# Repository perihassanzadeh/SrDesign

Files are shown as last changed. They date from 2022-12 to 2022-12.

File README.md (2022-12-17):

# Rubik's Cube Solver
System to automatically solve a Speed cube from any state

The system requirements were:
- Use Computer Vison to capture the current state of the cube
- Develop a non-trivial solving algorithm
- Use motors to actuate the faces of the cube to solve it

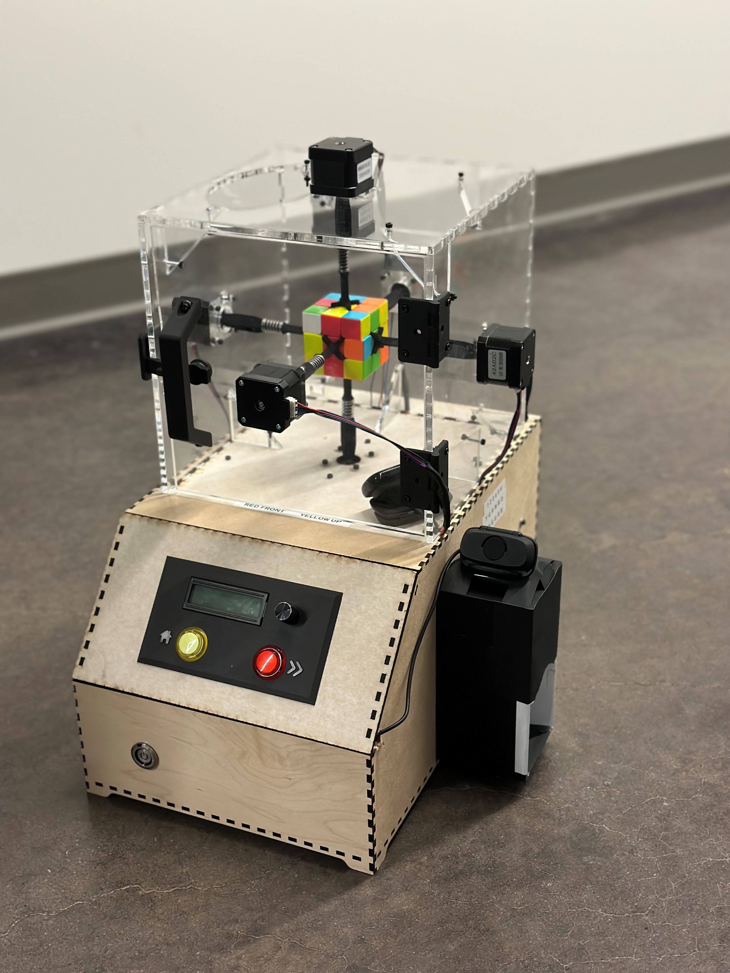
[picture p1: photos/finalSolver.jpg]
Final Prototype Optional title


# Key Features
- Computer Vision to Automatically Detect Current State
- CFOP Algorithm
- Simple User Interface (Auto-solve, Step-solve, Shuffle)
- Display each Move in Sequence
- Cube is Removable

# Demo
Video link coming soon

# Contributers
Peri Hassanzadeh, Alex Haver, Matt Meehan, Prosper Tjelmeland

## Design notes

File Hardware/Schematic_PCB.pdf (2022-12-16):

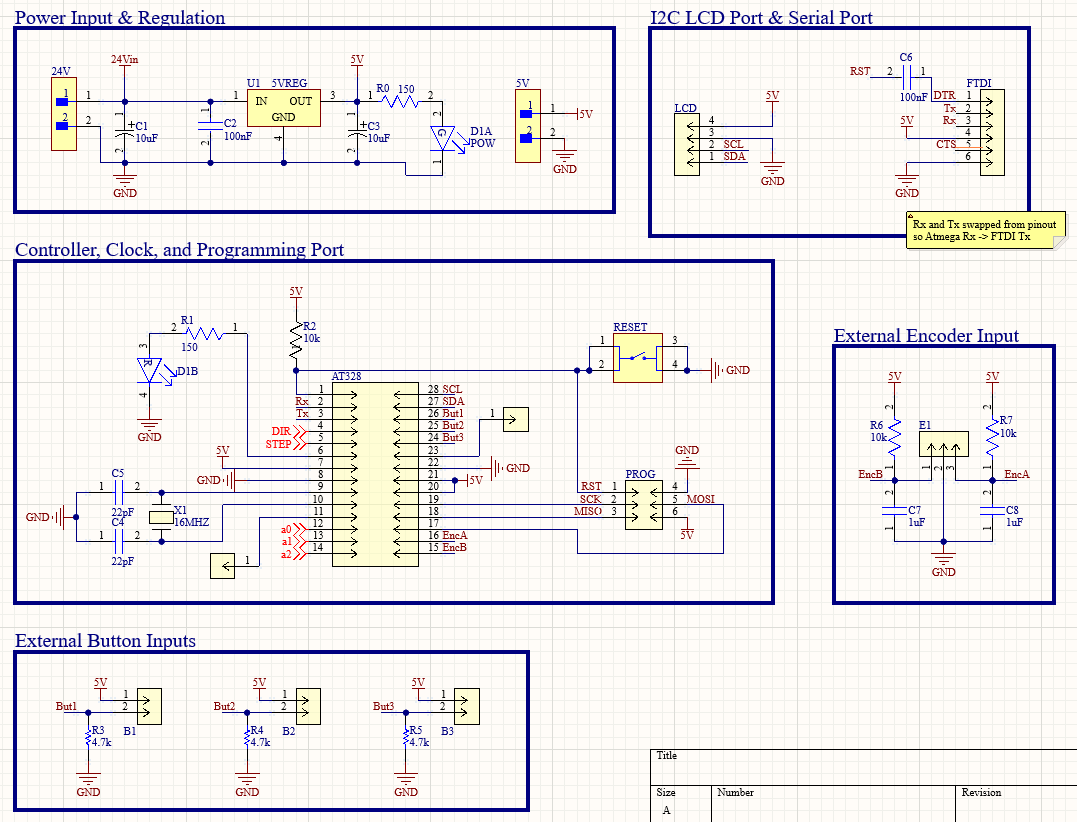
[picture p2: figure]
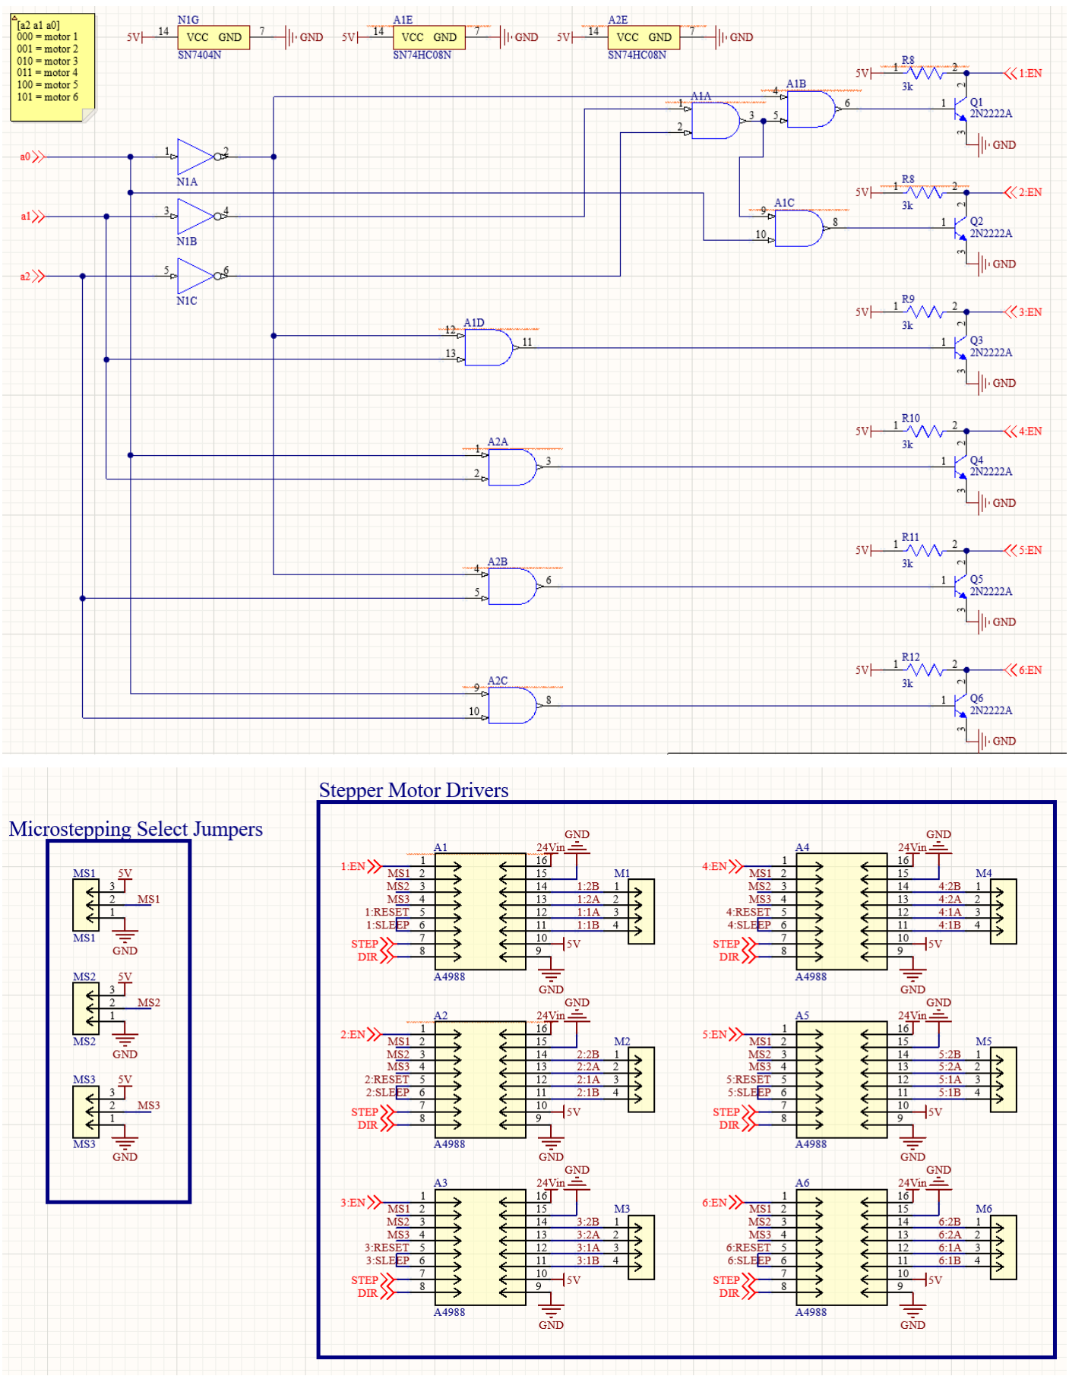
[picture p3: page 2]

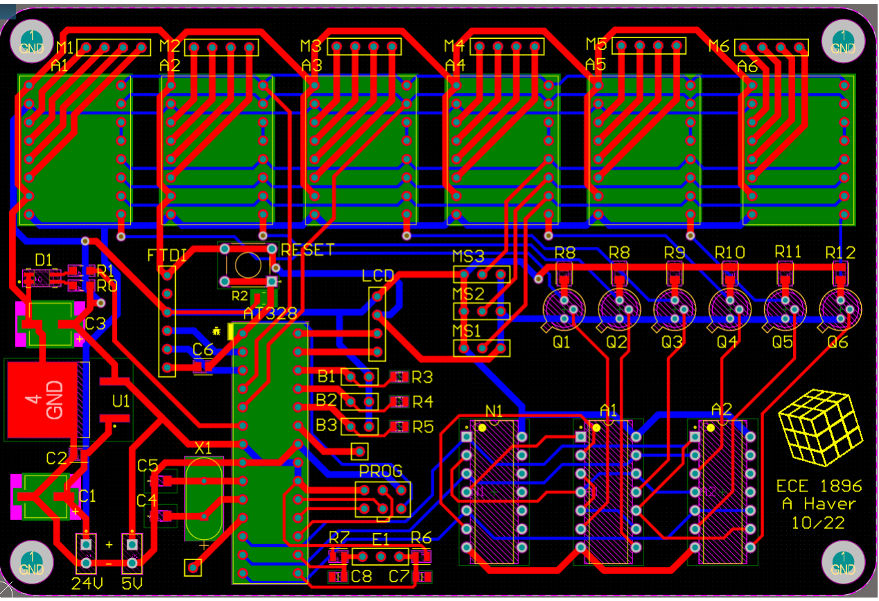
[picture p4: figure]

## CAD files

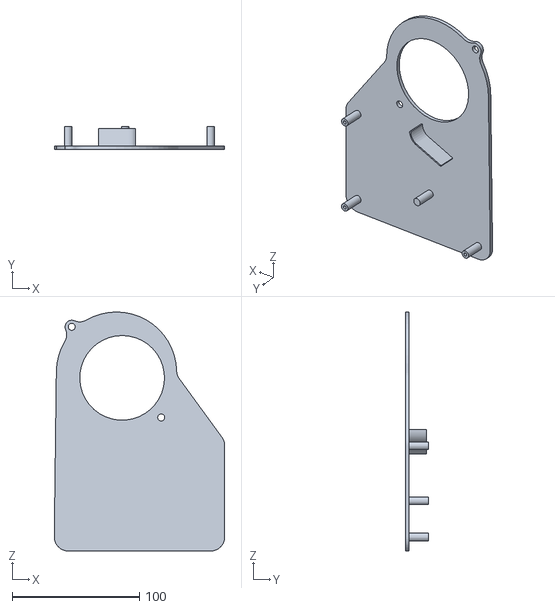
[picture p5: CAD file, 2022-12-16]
Hardware/CoolingBench.STL
133.9 x 18.3 x 187.7

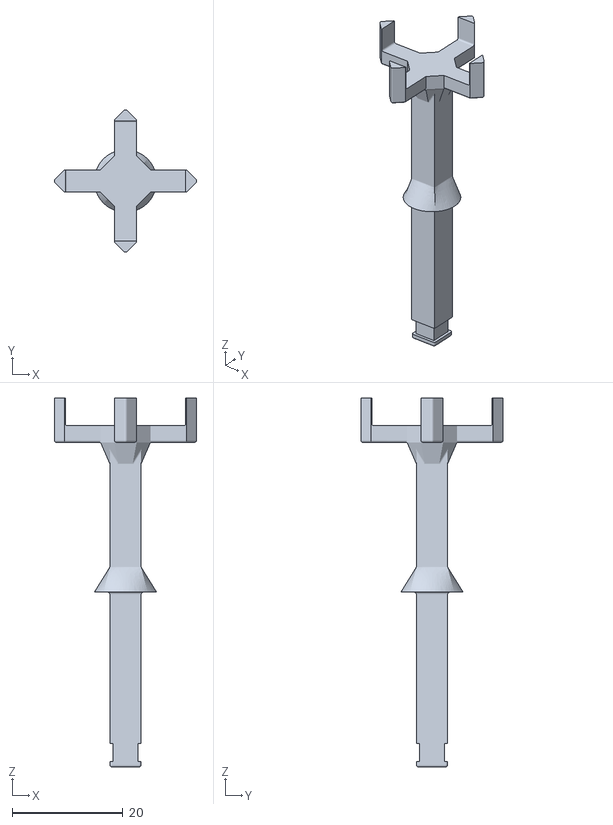
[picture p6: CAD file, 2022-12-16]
Hardware/SpringRod.STL
25.7 x 25.7 x 66.5

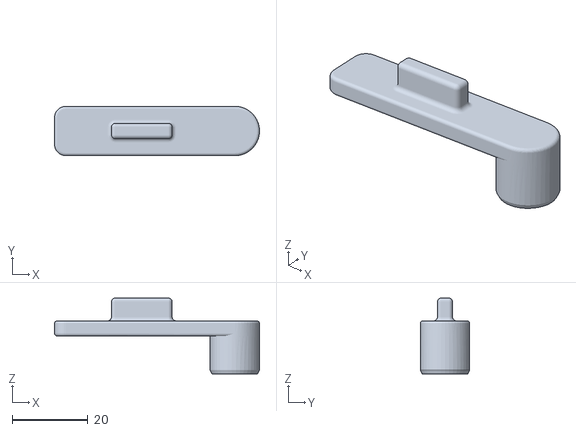
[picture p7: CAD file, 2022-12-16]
Hardware/LatchLever.STL
54.0 x 13.0 x 20.0

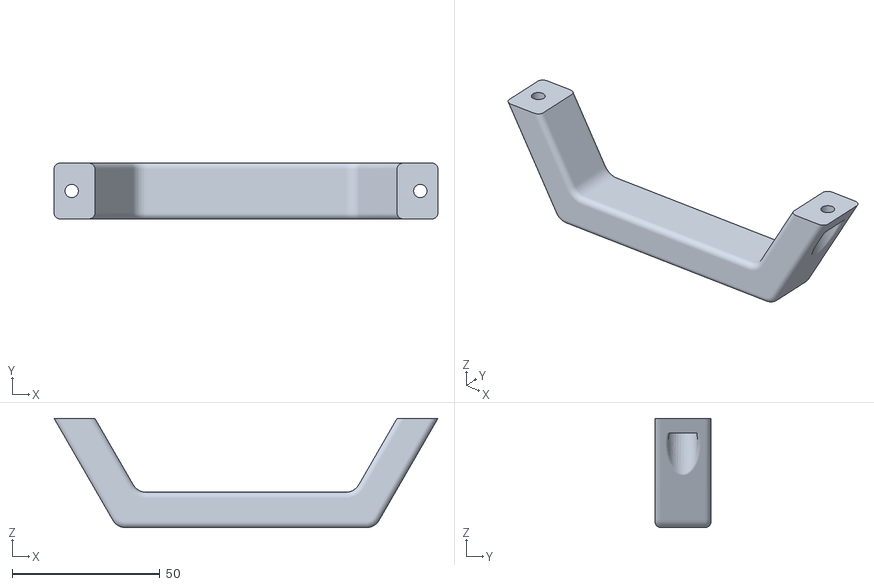
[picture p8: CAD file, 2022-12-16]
Hardware/RubiksHandle.STL
130.0 x 19.0 x 37.0

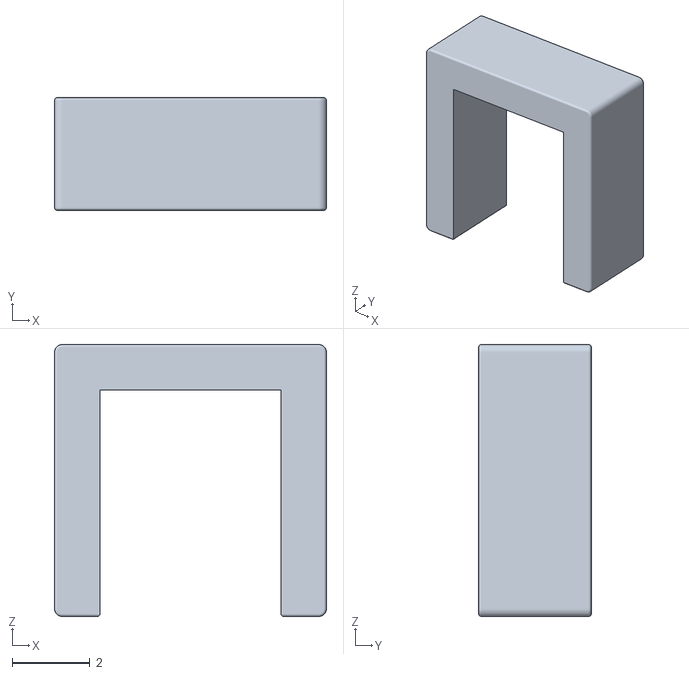
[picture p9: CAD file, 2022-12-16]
Hardware/SpringLock.STL
7.00 x 2.90 x 7.00

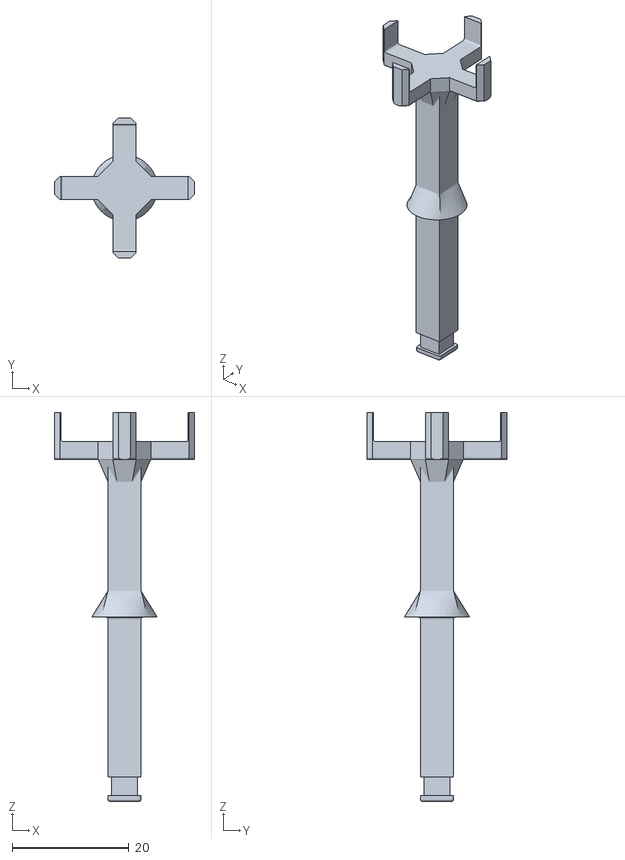
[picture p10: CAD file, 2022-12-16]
Hardware/sussusamogus.stl
24.0 x 24.0 x 66.5

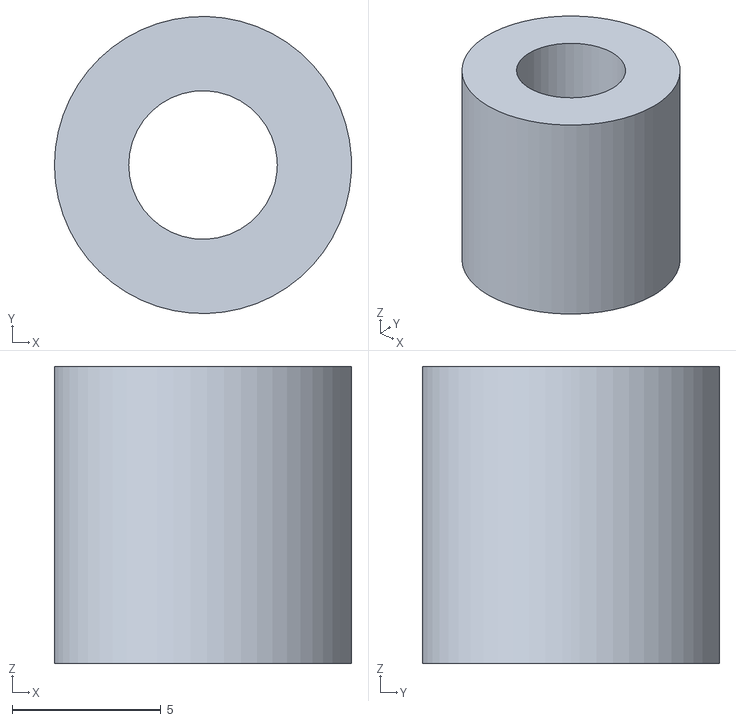
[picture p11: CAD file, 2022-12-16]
Hardware/RodTest.STL
10.0 x 10.00 x 10.0

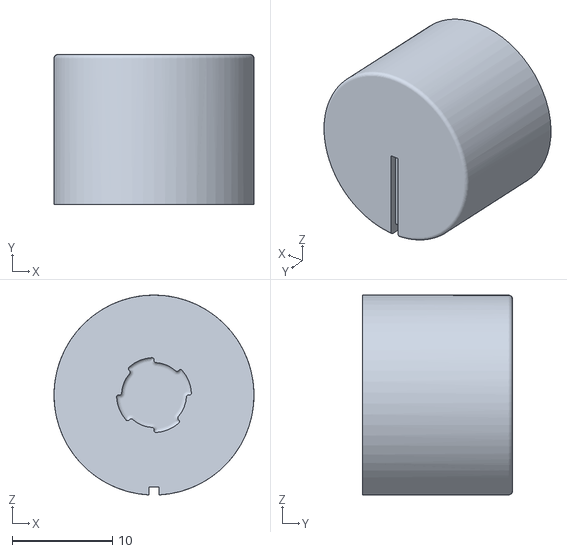
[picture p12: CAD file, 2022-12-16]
Hardware/Knob.STL
20.0 x 15.0 x 20.0

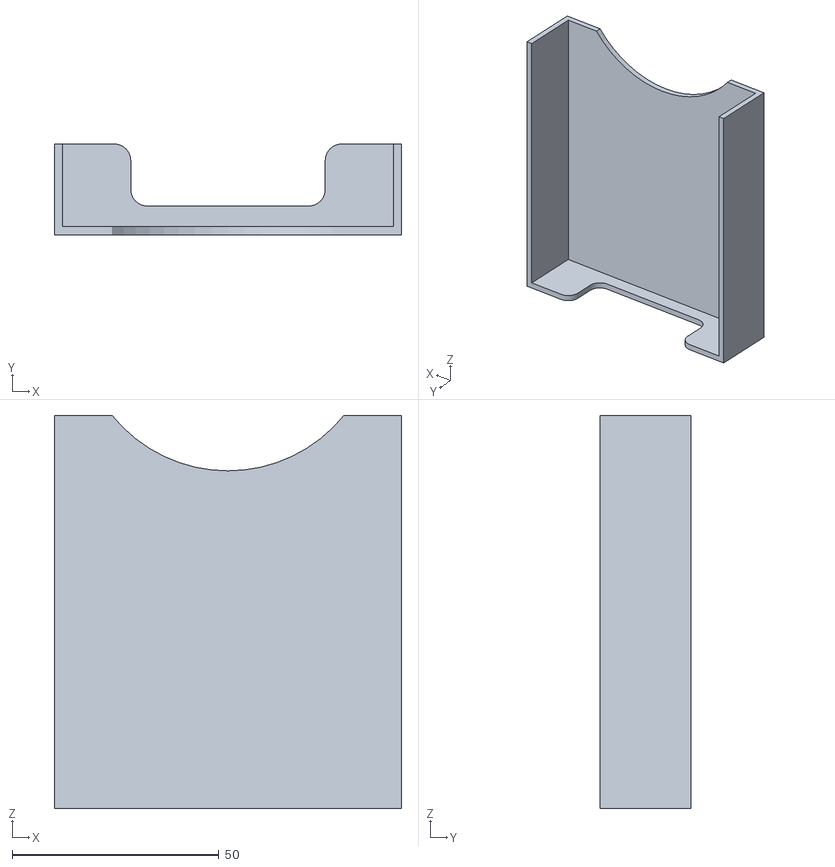
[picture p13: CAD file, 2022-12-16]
Hardware/ScanBoxShade.STL
84.0 x 22.0 x 95.0

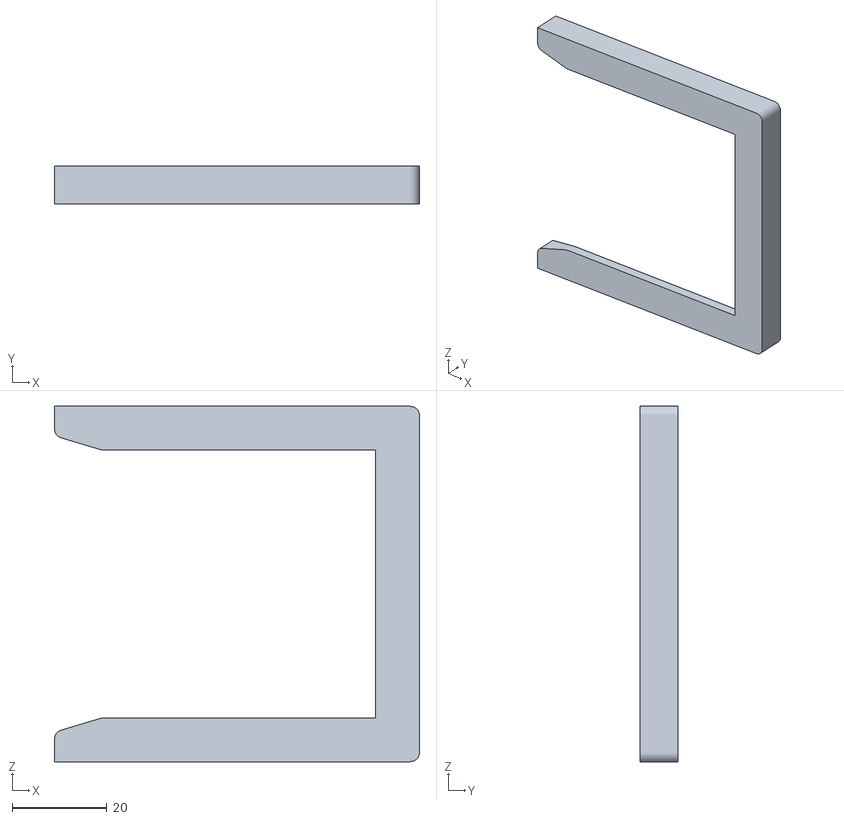
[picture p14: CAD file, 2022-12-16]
Hardware/CubeScanCenter.STL
77.0 x 8.00 x 75.0

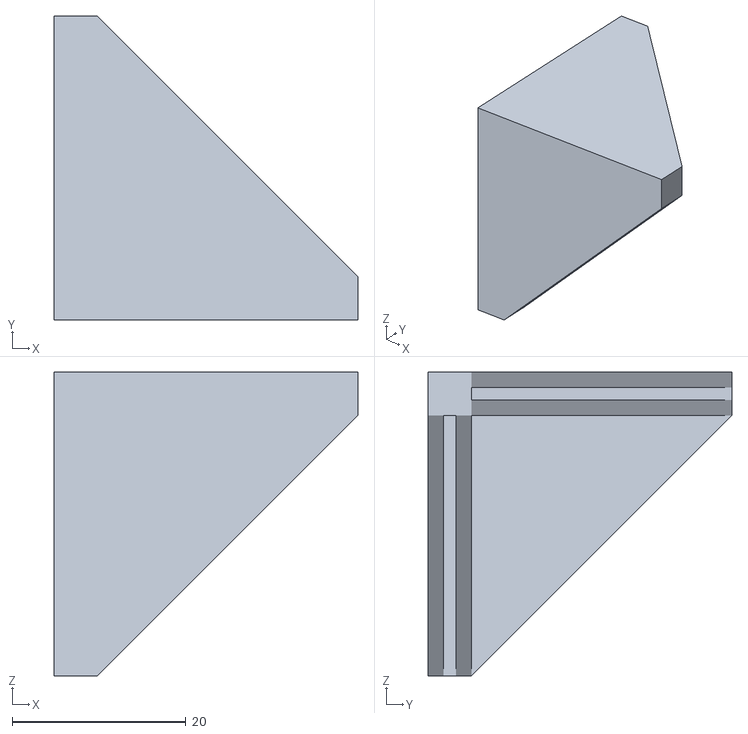
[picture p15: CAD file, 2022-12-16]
Hardware/CornerHolder_1.4mm.STL
35.0 x 35.0 x 35.0

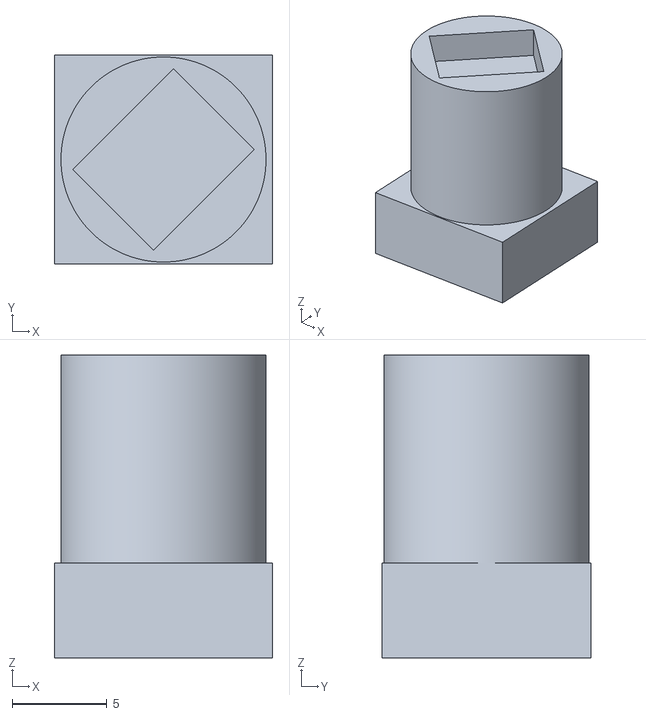
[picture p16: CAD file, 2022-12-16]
Hardware/SolenoidLockV6 1.stl
11.5 x 11.0 x 16.0

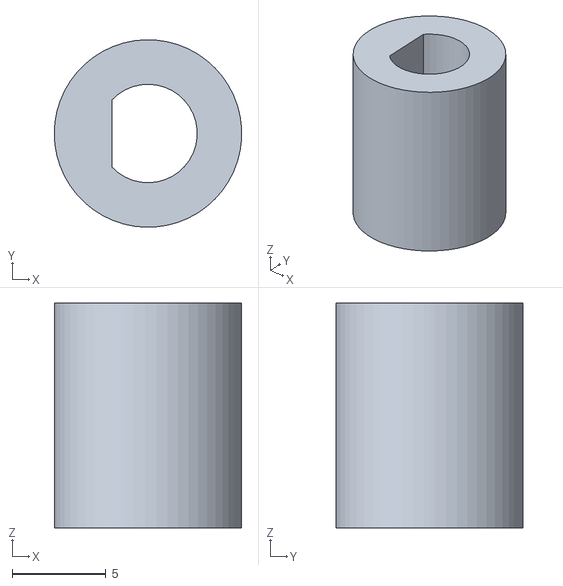
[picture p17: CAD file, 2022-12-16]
Hardware/ResinMotorTest.STL
10.0 x 10.00 x 12.0

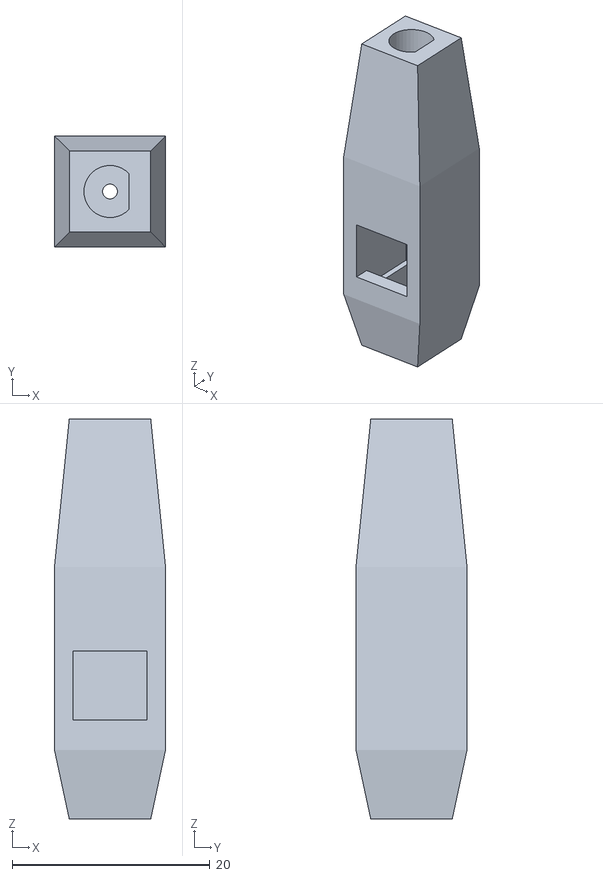
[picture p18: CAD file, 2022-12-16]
Hardware/SpringBase_Fixed.STL
11.2 x 11.2 x 40.5

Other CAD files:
Hardware/ResinRodTest.STL
Hardware/InterfaceBench.STL
Hardware/SpringBase_Resin2.STL
Hardware/CornerHolder.STL
Hardware/ArmLong_4.STL
Hardware/ArmMed_1.STL
Hardware/ArmShort_2.STL
Hardware/BenchStandoff.STL
Hardware/BottomBeam.STL
Hardware/CornerHolder_1.45mm.STL
Hardware/InterfacePanel_Final.STL
Hardware/LatchBody.STL
Hardware/LatchLever2.STL
Hardware/Ring.STL
Hardware/RodFingers.STL
Hardware/RodMotorAdapt.STL
Hardware/SolenoidTowerV6 1.stl
Hardware/StepShaftTest.STL
Hardware/cameraholder (1).stl
Hardware/curveclaw.stl

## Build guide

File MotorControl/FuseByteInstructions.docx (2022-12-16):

These instructions are for reading and writing the fuse bytes on an ATmega328 using the "USBtiny" / "USBtinyISP" programmer (Pocket AVR Programmer from Sparkfun)

Ensure latest version of avrdude-x.x-mingw32.zip is downloaded from:

http://download-mirror.savannah.gnu.org/releases/avrdude/

Navigate to the directory containing the downloaded avrdude.exe:

To view chip data:

avrdude -c usbtiny -p m328 -v

To view current fuse bytes:

avrdude.exe -c usbtiny -p m328

To write low fuse byte:

avrdude -c usbtiny -p m328 -U lfuse:w:0x##:m

To write high fuse byte to preserve EEPROM through chip erase:

avrdude -c usbtiny -p m328 -U hfuse:w:0xD6:m

Default fuses from chip: (E:FD, H:DE, L:FF)

Default fuses from datasheet?: (E:FF, H:D9, L:62)

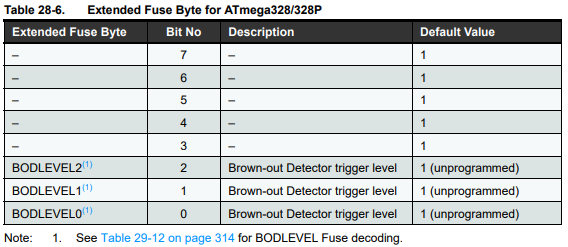
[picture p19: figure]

View datasheet here: ATmega48A/PA/88A/PA/168A/PA/328/P (https://ww1.microchip.com/downloads/aemDocuments/documents/MCU08/ProductDocuments/DataSheets/ATmega48A-PA-88A-PA-168A-PA-328-P-DS-DS40002061B.pdf)

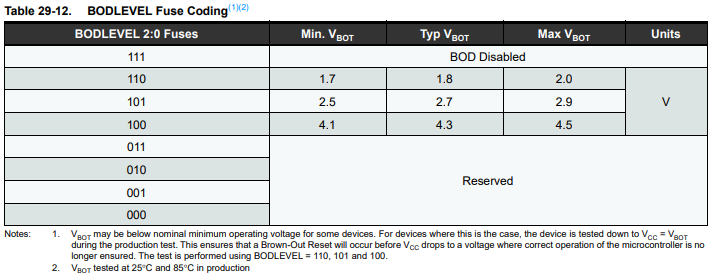
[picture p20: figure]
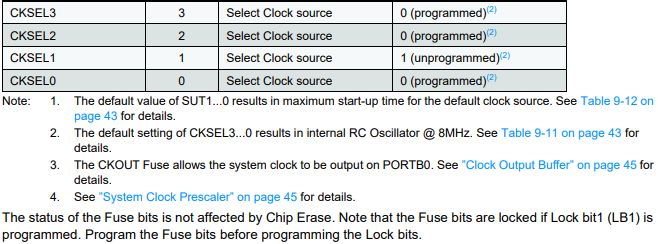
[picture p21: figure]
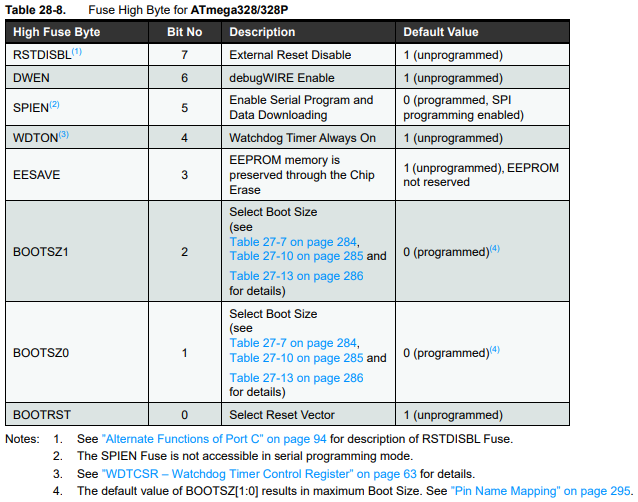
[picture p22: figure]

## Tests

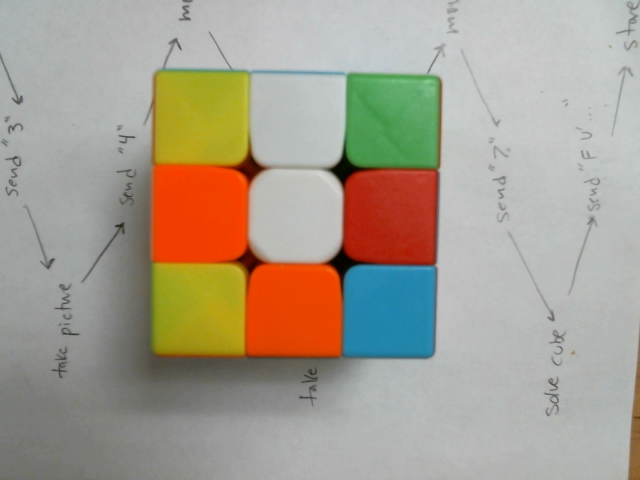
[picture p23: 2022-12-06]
ComputerVision/dynamTest15.png

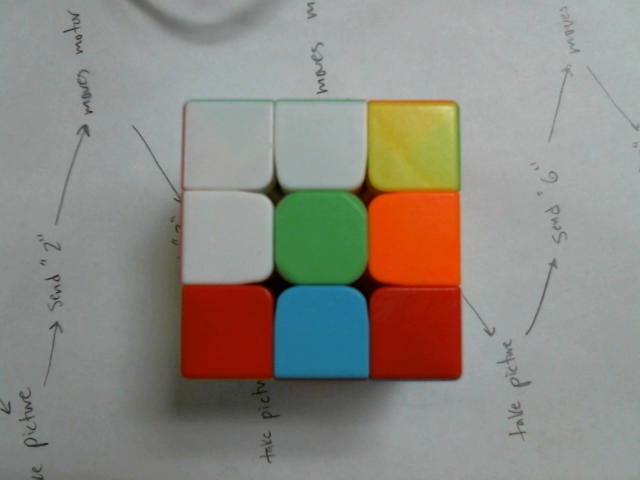
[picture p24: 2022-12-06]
ComputerVision/dynamTest1.png

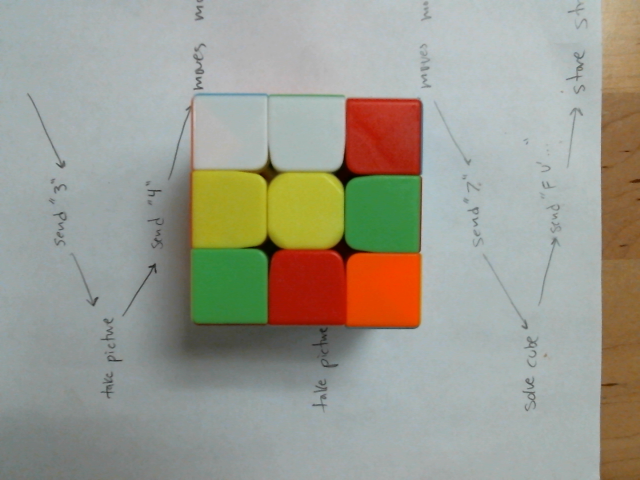
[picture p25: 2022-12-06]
ComputerVision/dynamTest18.png

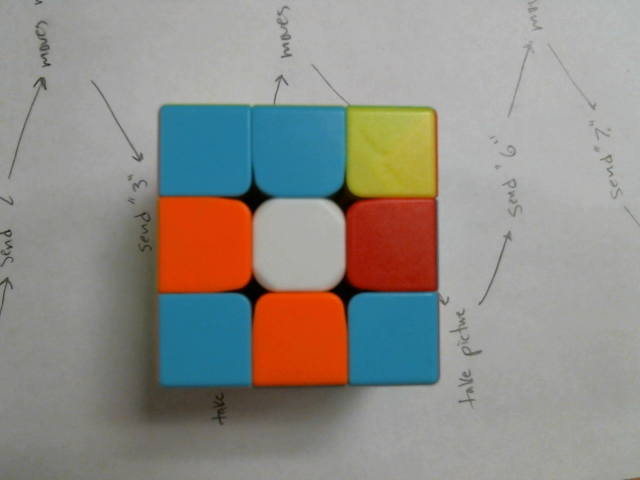
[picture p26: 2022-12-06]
ComputerVision/dynamTest3.png

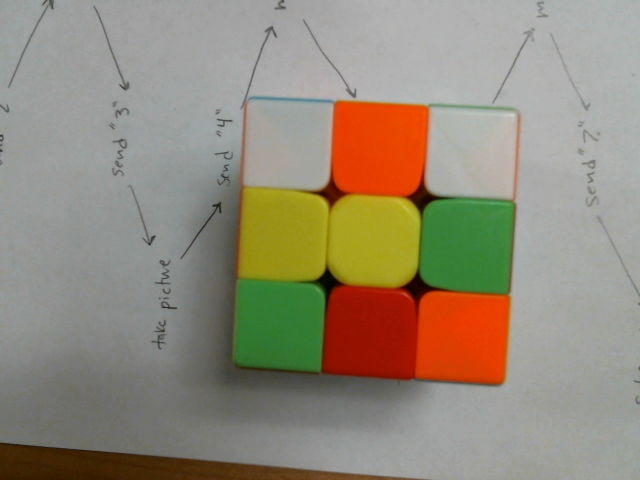
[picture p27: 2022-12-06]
ComputerVision/dynamTest12.png

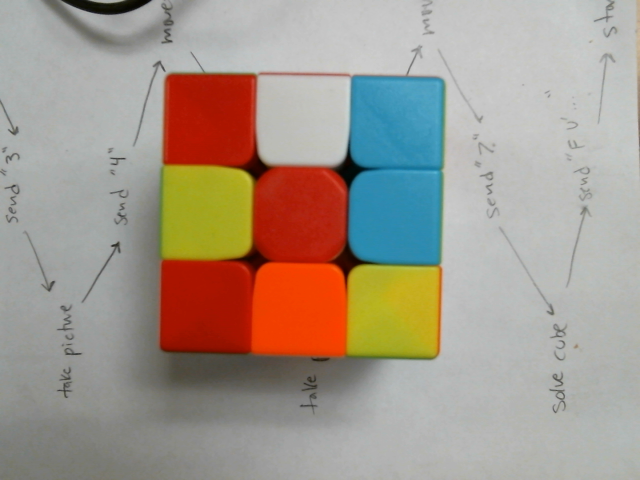
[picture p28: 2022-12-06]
ComputerVision/dynamTest8.png

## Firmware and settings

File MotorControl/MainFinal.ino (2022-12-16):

//U L F R B D U' L' F' R' B' D' U2 L2 F2 R2 B2 D2
#include <Arduino.h>
#include "A4988.h"
#include "DFRobot_RGBLCD1602.h"
#include "EEPROMex.h"
#include <Adafruit_NeoPixel.h>

//MOTOR CONTROL//
//PHYSICAL HARDWIRED CONTROL//
#define DIR 2  //pin 4
#define STEP 3 //pin 5
#define MOTOR_STEPS 200  // Motor steps per revolution
#define a0 6   //pin 12  //enable in binary
#define a1 7   //pin 13
#define a2 8   //pin 14
//SPEED CONTROL//
#define MAXRPM 1200  // MAXIMUM RPM for cruise speed
#define MAXACCEL 16000
#define MAXDECEL 16000
int RPM = 600;  //  set RPM for cruise speed
int ACCEL = 8000;  // Acceleration and deceleration values are always in FULL steps / s^2
int DECEL = 8000;
int percentMaxSpeed = 50;
#define MICROSTEPS 2

A4988 motor0(MOTOR_STEPS, DIR, STEP); //a = 000    //global motor objects
A4988 motor1(MOTOR_STEPS, DIR, STEP); //a = 001
A4988 motor2(MOTOR_STEPS, DIR, STEP); //a = 010
A4988 motor3(MOTOR_STEPS, DIR, STEP); //a = 011
A4988 motor4(MOTOR_STEPS, DIR, STEP); //a = 100
A4988 motor5(MOTOR_STEPS, DIR, STEP); //a = 101
A4988 motor6(MOTOR_STEPS, DIR, STEP); //a = 110

//LCD SCREEN//
DFRobot_RGBLCD1602 lcd(16, 2); //global lcd object
byte debug[8] = {
    0b10101,
    0b01110,
    0b11011,
    0b01110,
    0b10001,
    0b00000,
    0b00000,
    0b00000
    };
byte home[8] = {
    0b00100,
    0b01110,
    0b11111,
    0b11111,
    0b11011,
    0b11011,
    0b00000,
    0b00000
    };
byte shuffle[8] = {
    0b01000,
    0b11111,
    0b01000,
    0b00010,
    0b11111,
    0b00010,
    0b00000,
    0b00000
    };
byte scan[8] = {
    0b00000,
    0b11011,
    0b10001,
    0b00100,
    0b10001,
    0b11011,
    0b00000,
    0b00000
    };
byte solve[8] = {
    0b00010,
    0b00100,
    0b01110,
    0b00100,
    0b01000,
    0b00000,
    0b00000,
    0b00000
    };
byte leftArrow[8] = {
    0b00010,
    0b00100,
    0b01000,
    0b11111,
    0b01000,
    0b00100,
    0b00010,
    0b00000
    };
byte checkMark[8] = {
    0b00000,
    0b00001,
    0b00010,
    0b10100,
    0b01000,
    0b00000,
    0b00000,
    0b00000
    };

//BUTTONS//
#define button1 A3   //pin 26
#define button2 A2   //pin 25
volatile bool B1Flag = 0;  //Flags to be used by interrupt - goes high (1) when button is pushed
volatile bool B2Flag = 0;
volatile unsigned long lastPushTime1;  //based off millis() - can run up to 50 days
volatile unsigned long lastPushTime2;
#define button1Led A0  //pin 23
#define button2Led 5  //pin 11

//ENCODER BUTTON
#define buttonE A1   //pin 24
volatile bool BEFlag = 0;
volatile unsigned long lastPushTimeE;

//ENCODER
#define EncA 10  //pin 16
#define EncB 9   //pin 15
volatile bool CWFlag = 0;  //Clockwise flag  -  goes high when encoder rotated clockwise
volatile bool CCWFlag = 0;  //Counter-clockwise flag ...


//SYSTEM VARIABLES//
#define led 4  //onboard led  //pin 6
//FSM
enum STATES {Skip, Debug, Home, Shuffle, Scan, Presolve, Solve};
STATES state = Home; //start at home
STATES stateLoop;
//TIMERS
int Timer1AVal; //button1 led count value  //number of wave toggles - set to 2x num of square waves wanted,  -1 for infinite (stop with TIMSK1 |= (0 << OCIE1A);)
int Timer1BVal; //button2 led count value
//ENCODER
int lineSelected; //used for item selection in menu
//RANDOM SHUFFLE SEED
uint32_t oldSeed;
uint32_t seed;
//SCAN SEQUENCE RECIEVED
bool scanned = 0; //track if scanned yet, set to 0 since it hasn't scanned yet when powered up
String inputSequence = "";
String moves[60]; //all moves read from serial
int movesLength = 0;
//AUTO-SOLVE or STEP-SOLVE
bool solveType = 0; //set to auto solve by default
int currentPosition = 0;  //keep track of current move for step-solve mode
//DEBUG
int debugMotorSelect = 0;  //for testing
//LED ring
Adafruit_NeoPixel pixels(12, 12, NEO_GRB + NEO_KHZ800); //12 leds on pin 12


void setup() {
  //START SERIAL PORT//
  Serial.begin(9600);

  //LCD SCREEN INITIALIZATION//
  lcd.init();
  lcd.setRGB(100, 100, 100);
  lcd.customSymbol(0, debug);
  lcd.customSymbol(1, home);
  lcd.customSymbol(2, shuffle);
  lcd.customSymbol(3, scan);
  lcd.customSymbol(4, solve);
  lcd.customSymbol(5, leftArrow);
  lcd.customSymbol(6, checkMark);

  //MOTOR OUTPUT PIN DEFINITIONS//
  pinMode(STEP, OUTPUT);
  pinMode(DIR, OUTPUT);
  pinMode(a0, OUTPUT);
  pinMode(a1, OUTPUT);
  pinMode(a2, OUTPUT);
  motor0.begin(RPM, MICROSTEPS);
  motor0.setSpeedProfile(motor0.LINEAR_SPEED, ACCEL, DECEL);
  motor1.begin(RPM, MICROSTEPS);
  motor1.setSpeedProfile(motor1.LINEAR_SPEED, ACCEL, DECEL);
  motor2.begin(RPM, MICROSTEPS);
  motor2.setSpeedProfile(motor2.LINEAR_SPEED, ACCEL, DECEL);
  motor3.begin(RPM, MICROSTEPS);
  motor3.setSpeedProfile(motor3.LINEAR_SPEED, ACCEL, DECEL);
  motor4.begin(RPM, MICROSTEPS);
  motor4.setSpeedProfile(motor4.LINEAR_SPEED, ACCEL, DECEL);
  motor5.begin(RPM, MICROSTEPS);
  motor5.setSpeedProfile(motor5.LINEAR_SPEED, ACCEL, DECEL);

  //BUTTON INPUT PIN DEFINTIONS AND INTERRUPTS// - (PIN CHANGE INTERRUPT)
  pinMode(button1, INPUT);  //using an external 4.7k pulldown resistor
  pinMode(button2, INPUT);
  pinMode(buttonE, INPUT);
  PCICR |= B00000010;  //Enable pin change interrupt on port C (A0-A5) (pins 23-28)
  PCMSK1 |= B00001110;  //Enable interrupts for pins A0-A2 (pins 24-26)

  //BUTTON LEDs
  pinMode(button1Led, OUTPUT);
  pinMode(button2Led, OUTPUT);
  //ONBOARD LED
  pinMode(led, OUTPUT);

  //ENCODER INPUT PIN DEFINTIONS, INTERRUPTS, AND POSITION CONFIG//
  pinMode(EncA, INPUT);  //using an external 10k pullup resistor
  pinMode(EncB, INPUT);
  PCICR |= B00000001;  //Enable pin change interrupt on port B (D8-D13) (pins 14-19)
  PCMSK0 |= B00000100;  //Enable interrupts for pin D10 (pins 16, EncA)


  //SYSTEM
  //Timer 1 for button1 and 2 blink led
  Timer1Config(0.9);  //config timer1 @ 0.9 Hz

  //init LED ring
  pixels.begin();

  //startup dance
  lcd.setCursor(2, 0);
  lcd.print("Rubik's Cube");
  lcd.setCursor(5, 1);
  lcd.print("Solver");

  startupShow();

  lcd.setRGB(100, 100, 100); //set to white for normal operation

  //start LED ring
  pixels.clear();
  for(int i=0; i<12; i++)  //12 pixels
    pixels.setPixelColor(i, pixels.Color(10, 10, 10));
  pixels.show();
}


void loop() 
{

  //STATE TRANSITION - runs once like setup() but using flags
  switch(state)
  {
    case Debug://*******************************************************************************************//
      lcd.clear();
      lcd.setCursor(15, 0);
      lcd.write((unsigned char)0);  //debug symbol
    
      blinkStop(); //stop button blinking

      lcd.setCursor(0, 0);
      lcd.print("Time:");
      lcd.setCursor(10, 0);
      lcd.print("E:");
      lcd.print(EEPROM.readLong(0));
      lcd.setCursor(0, 1);
      lcd.print("Btn:"); 
      lcd.setCursor(7, 1);
      lcd.print("Spe:");
      lcd.print(percentMaxSpeed); 
      lcd.setCursor(15, 1);
      lcd.print(debugMotorSelect);
      stateLoop = state;  //begin state loop and reset transition flag
      state = Skip;
      break;
    case Home://*******************************************************************************************//
      lcd.clear();
      lcd.setCursor(15, 0);
      lcd.write((unsigned char)1);  //home symbol

      if(scanned){
        lcd.setCursor(14, 1);
        lcd.write((unsigned char)6); //check mark
        lcd.write((unsigned char)3);  //display scan symbol if scan has been completed
      }

      blinkStop(); //stop button blinking

      lcd.setCursor(0, 0);
      lcd.write((unsigned char)2);  //shuffle
      lcd.print("Shuffle ");
      lcd.write((unsigned char)5);  //left arrow
      lcd.print("-");
      lcd.setCursor(0, 1);
      if(scanned){ //display solve if already scanned
        lcd.write((unsigned char)4);
        lcd.print("Solve");
      }
      else{ //display scan if not yet scanned
        lcd.write((unsigned char)3);
        lcd.print("Scan");
      }

      //variable lcd output handled below
      lineSelected = 0;
      
      stateLoop = state;
      state = Skip;
      break;
    case Shuffle://*******************************************************************************************//
      lcd.clear();
      lcd.setCursor(15, 0);
      lcd.write((unsigned char)2);  //shuffle symbol

      blinkStop(); //stop button blinking
      blinkRed(-1);  //blink red indefinitely
      
      oldSeed = EEPROM.readLong(0); //retrieve old seed from address 0
      seed = oldSeed + 1;
      EEPROM.updateLong(0, seed);  //write (update) incemented seed back into address 0 (store seed to be used) 
      lcd.setCursor(0, 0);
      lcd.print("Seed:");
      
      randomSeed(seed); 
      lcd.print(random(0,2147483647), HEX);     //seed representation
      
      lcd.setCursor(3, 1);
      lcd.print("Push to start");
      
      stateLoop = state;
      state = Skip;
      break;
    case Scan://*******************************************************************************************//
      lcd.clear();
      lcd.setCursor(15, 0);
      lcd.write((unsigned char)3);  //scan symbol

      blinkStop(); //stop button blinking
      blinkRed(-1);

      lcd.setCursor(0, 0);
      lcd.print("Scan");

      lcd.setCursor(3, 1);
      lcd.print("Push to start");

      stateLoop = state;
      state = Skip;
      break;
    case Presolve://*******************************************************************************************//
      lcd.clear();
      lcd.setCursor(15, 0);
      lcd.write((unsigned char)4);  //solve symbol

      blinkStop(); //stop button blinking

      //autosolve or stepsolve
      lcd.setCursor(0, 0);
      lcd.print("Auto-Solve ");
      lcd.write((unsigned char)5);  //left arrow
      lcd.print("-");

      lcd.setCursor(0, 1);
      lcd.print("Step-Solve");

      lineSelected = 0; //select autosolve as default
      solveType = 0; 

      stateLoop = state;
      state = Skip;
      break;
    case Solve://*******************************************************************************************//
      lcd.clear();
      lcd.setCursor(15, 0);
      lcd.write((unsigned char)4);  //solve symbol

      blinkStop(); //stop button blinking

      if(solveType){ //if step-solve
        lcd.setCursor(0, 0);
        lcd.print("Step-Solve");
        lcd.setCursor(0, 1);
        lcd.print("Step: ");
        lcd.print(moves[0]);

        lcd.setCursor(10, 1);
        lcd.print("1/");
        lcd.print(movesLength);
        lcd.print("  ");

        currentPosition = 0;  //start at step 0
        percentMaxSpeed = 50;    //set step solve to 50% speed always
        setMotorSpeeds(percentMaxSpeed);
      }
      else{ //if auto-solve
        blinkRed(-1);

        lcd.setCursor(0, 0);
        lcd.print("Speed:");
        lcd.print(percentMaxSpeed); 
        lcd.print("% ");

        lcd.setCursor(3, 1);
        lcd.print("Push to start");
      }


      stateLoop = state;
      state = Skip;
      break;
    default://*******************************************************************************************//
      //DO NOTHING if not transitioning (when state == Skip, set after passes through once)
      break;
  }

  //STATE LOGIC/OUTPUT - like loop() //**//**//**//**//**//**//**//**//**//**//**//**//**//**//**//**//**//**//**//**//**//**//**//**//**//**//**//**//**//**//**//**//**//**//**//**//**//**//**//**//**//**//
  switch(stateLoop)
  {
    case Debug://**/////////////////////////////////////////////////////////////////////////////////////////**
      lcd.setCursor(5, 0);  //for test debugging - display seconds in bottom left of screen
      lcd.print(millis()/1000); //print seconds since startup

      //EXIT DEBUG (don't use home button)
      if(CCWFlag && digitalRead(button1) && digitalRead(button2)){    //home button cycles through selected motor
        state = Home;                                                 //forward button cycles through selected speed
        CCWFlag = 0;                                                  //encoder rotates motor CW or CCW
      }

      //ENCODER HANDLERS
      if(CWFlag){  //if encoder is rotates clockwise
        rotateMotor90(debugMotorSelect, 0); //CW    -just for testing
        CWFlag = 0;  //reset flag for next time
      }
      if(CCWFlag){
        rotateMotor90(debugMotorSelect, 1);  //CCW
        CCWFlag = 0;  //reset flag for next time
      }

      //PUSH BUTTON HANDLERS
      if(B1Flag && Timer1AVal == 0){ //if button is pushed and timer is ready to output wave (avoids a rare led always on state)
        lcd.setCursor(4,1);
        lcd.print("1");
        blinkYellow(2);
        debugMotorSelect = (debugMotorSelect+1)%6;
        lcd.setCursor(15, 1);
        lcd.print(debugMotorSelect);
        B1Flag = 0;
      }
      if(B2Flag && Timer1BVal == 0){
        lcd.setCursor(4,1);
        lcd.print("2");
        blinkRed(2);
        percentMaxSpeed = (percentMaxSpeed%100)+5;
        setMotorSpeeds(percentMaxSpeed);
        lcd.setCursor(11,1);
        lcd.print(percentMaxSpeed);
        if(percentMaxSpeed != 100)
          lcd.print("  ");  //might be shorter number
        B2Flag = 0;
      }
      if(BEFlag){
        lcd.setCursor(4,1);
        lcd.print("E");
        BEFlag = 0;
      }

      break;
    case Home://**/////////////////////////////////////////////////////////////////////////////////////////**

      if(CCWFlag && digitalRead(button1) && digitalRead(button2)){
        state = Debug;
        CCWFlag = 0;
      }
      if(CCWFlag)
      {
        lineSelected = 0;
        lcd.setCursor(9, 0);
        lcd.write((unsigned char)5);  //left arrow
        lcd.print("-");
        lcd.setCursor(9, 1);
        lcd.print("  ");
        CCWFlag = 0;
      }
      if(CWFlag)
      {
        lineSelected = 1;
        lcd.setCursor(9, 0);
        lcd.print("  ");
        lcd.setCursor(9, 1);
        lcd.write((unsigned char)5);  //left arrow
        lcd.print("-");
        CWFlag = 0;
      }

      //PUSH BUTTON HANDLERS
      if(B1Flag)
        B1Flag = 0;  //must handle flags so they aren't processed in next state
      if(B2Flag)
        B2Flag = 0;

      if(BEFlag){
        if(scanned){ //if already scanned, is displaying solve and should transition to solve
          if(lineSelected == 0) //first line = shuffle
            state = Shuffle;
          else
            state = Presolve;
        }
        else{ //hasnt been scanned and should transition to scan
          if(lineSelected == 0) //first line = shuffle
            state = Shuffle;
          else
            state = Scan;
        }
        BEFlag = 0;
      }
      
      break;
    case Shuffle://**/////////////////////////////////////////////////////////////////////////////////////////**

      if(CWFlag)
        CWFlag = 0;
      if(CCWFlag)
        CCWFlag = 0;

      if(B1Flag){ //transition home
        state = Home;
        B1Flag = 0;
      }
    
      if(B2Flag){ //button to start shuffling
        blinkStop(); //stop button blinking
        digitalWrite(button2Led, HIGH); //turn button solid

        setMotorSpeeds(90);
        
        //generate 22 random moves
        for(int i = 0; i < 23; i++){
          int num = random(0,12); //0,1,2,3,4,5,6,7,8,9,10,11 (8.33%) (CW & CCW for each of 6 faces)

          lcd.setCursor(0, 1); //display current shuffle move to screen
          lcd.print("Motor ");
          lcd.print(num/2);
          lcd.print(" ");
          if(num%2)
            lcd.print("CW      ");
          else
            lcd.print("CCW     ");

          rotateMotor90(num/2, num%2);  //uses core motor rotate fcn //0,1,2,3,4,5  (16.67%)  ,   //0,1 (50%) //0=CW, 1=CCW
        }

        scanned = 0; //must rescan if shuffled
        inputSequence = "";
        memset(moves, "", sizeof(moves)); //clear moves
        state = Home;
        B2Flag = 0;
      }

      if(BEFlag)
        BEFlag = 0;
      
      break;
    case Scan://**/////////////////////////////////////////////////////////////////////////////////////////**
      
      if(CWFlag)
        CWFlag = 0;
      if(CCWFlag)
        CCWFlag = 0;

      if(B1Flag){ //transition home
        state = Home;
        B1Flag = 0;
      }

      
      if(B2Flag){ //button to start scan
        blinkStop(); //stop button blinking
        digitalWrite(button2Led, HIGH); //turn button solid

        Serial.println("1"); //send serial command to begin scan

        lcd.setCursor(0, 0);
        lcd.print("Starting scan   ");
        lcd.setCursor(0, 1);
        lcd.print("                ");

        lcd.setCursor(0, 1);
        for(int i = 0; i < 16; i++){  //print loading bar
          lcd.print(">");
          delay(100);
        }

/*
        //WAIT FOR SERIAL STRING COMMAND//
        while (Serial.available() == 0) {  //wait (loop) for serial string data available
          lcd.setCursor(0, 0);
          lcd.print("Waiting serial");
          delay(10000);
          if(B1Flag){  //if home button pushed while waiting - transition home
            state = Home;
            B1Flag = 0;
            break;
          }
        }   

        if(state != Home){ //if home button wasn't pushed to exit loop - read in scan
          inputSequence = "";
          inputSequence = Serial.readString();   //read until timeout
          inputSequence.trim(); 

          lcd.setCursor(0, 0);
          lcd.print(Serial.readString());
          delay(10000);

          splitInputString(inputSequence);

          scanned = 1;
          state = Home;
        }
        */
        inputSequence = "";
        Serial.setTimeout(30000); //set timeout to 30 sec
        inputSequence = Serial.readString();   //read until timeout
        inputSequence.trim(); 

        lcd.setCursor(0, 0);
        lcd.print(Serial.readString());
        delay(10000);

        splitInputString(inputSequence);

        scanned = 1;
        state = Home;

        B2Flag = 0;
      }
      
/*
      if(B2Flag){ //button to start scan
        B2Flag = 0;
        blinkStop(); //stop button blinking
        digitalWrite(button2Led, HIGH); //turn button solid

        Serial.println("1"); //send serial command to begin scan

        lcd.setCursor(0, 0);
        lcd.print("Starting scan   ");
        lcd.setCursor(0, 1);
        lcd.print("                ");

        while (Serial.available() == 0) {  //wait (loop) for serial string data available
          if(B1Flag){  //if home button pushed while waiting - transition home
            state = Home;
            B1Flag = 0;
            break;
          }
        } 

        String inputChar = "";
        inputChar = Serial.readString();   //wait here for "2"
        inputChar.trim(); 
        if(inputChar == "2"){
          
          rotateMotor("2D");
          rotateMotor("2L");
          rotateMotor("2U");
          rotateMotor("R");
          rotateMotor("L'");
          rotateMotor("2U");
          rotateMotor("2R");
          rotateMotor("2L");
          rotateMotor("2U");
          rotateMotor("R");
          rotateMotor("L'");
          rotateMotor("2D");
          
          Serial.println("3");

          while (Serial.available() == 0) {  //wait (loop) for serial string data available
            if(B1Flag){  //if home button pushed while waiting - transition home
              state = Home;
              B1Flag = 0;
              break;
            }
          } 

          inputChar = "";
          inputChar = Serial.readString();   //wait here for "4"
          inputChar.trim(); 
          if(inputChar == "4"){
            
            rotateMotor("2D");
            rotateMotor("L");
            rotateMotor("R'");
            rotateMotor("2U");
            rotateMotor("2L");
            rotateMotor("2R");
            rotateMotor("2U");
            rotateMotor("L");
            rotateMotor("R'");
            rotateMotor("2U");
            rotateMotor("2B");
            rotateMotor("2R");
            rotateMotor("2L");
            rotateMotor("2B");
            rotateMotor("2R");
            rotateMotor("2L");
            rotateMotor("2B");
            rotateMotor("2F");
            
            Serial.println("5");

            while (Serial.available() == 0) {  //wait (loop) for serial string data available
              if(B1Flag){  //if home button pushed while waiting - transition home
                state = Home;
                B1Flag = 0;
                break;
              }
            } 

            inputChar = "";
            inputChar = Serial.readString();   //wait here for "6"
            inputChar.trim(); 
            if(inputChar == "6"){
              
              rotateMotor("2F");
              rotateMotor("2B");
              rotateMotor("2L");
              rotateMotor("2R");
              rotateMotor("2B");
              rotateMotor("2L");
              rotateMotor("2R");
              rotateMotor("2B");
              rotateMotor("2L");
              rotateMotor("2R");
              
              Serial.println("7");

              while (Serial.available() == 0) {  //wait (loop) for serial string data available
                if(B1Flag){  //if home button pushed while waiting - transition home
                  state = Home;
                  B1Flag = 0;
                  break;
                }
              } 

              inputSequence = "";
              inputSequence = Serial.readString();   //read until timeout
              inputSequence.trim(); 
              splitInputString(inputSequence);

              scanned = 1;
              state = Home;

            }
            else
              break;

          }
          else
            break;

        }
        else
          break;

      }
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

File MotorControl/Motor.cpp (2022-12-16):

#include <Arduino.h>
#include "Motor.h"

#define microStep 16;

//create motor object enable pins (a2 a1 a0) represent the binary value of the motor
Motor::Motor(bool a2, bool a1, bool a0){
  a2EN = a2;
  a1EN = a1;
  a0EN = a0;
}

//create motor object and also assign frequency (speed) and degrees (rotation amount)
Motor::Motor(bool a2, bool a1, bool a0, double percentage, double degrees){
  a2EN = a2;
  a1EN = a1;
  a0EN = a0;
  double frequency = percentage;
  highTime = (1/frequency)/2;
  stepCount = 200 * (degrees/360) * microStep; //200 steps = 360 degrees
}

//adjusts speed of motor by change the frequency at which the square wave is send to the driver
void Motor::setSpeed(double percentage){
  double frequency = percentage;
  highTime = (1/frequency)/4; 
}

//adjusts the number of square waves sent to the driver (number of steps)
void Motor::setDegrees(double degrees){
  stepCount = 200 * (degrees/360) * microStep; //200 steps = 360 degrees
}

//rotates motor in direction specified by dir. TRUE = clockwise, FALSE = counterclockwise
void Motor::rotate(bool dir){
  digitalWrite(6, a0EN); //enable proper motor driver through combinational logic
  digitalWrite(7, a1EN);
  digitalWrite(8, a2EN);

  digitalWrite(2, dir); //configure direction pin for motor driver

  for(int i = 0; i < stepCount; i++){  //send square wave to stepper driver based on stepCount and highTime
    digitalWrite(3, HIGH);
    delay(highTime*1000/10);    //delay is in ms -> x1000
    digitalWrite(3, LOW);
    delay(highTime*1000/10);  //always 50% duty cycle
  }

}

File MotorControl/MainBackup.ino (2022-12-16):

//U L F R B D U' L' F' R' B' D'
#include "Motor.h"
#include "DFRobot_RGBLCD1602.h"

//MOTOR CONTROL//
#define dirPin 2  //pin 4
#define stepPin 3 //pin 5
#define a0Pin 6   //pin 12
#define a1Pin 7   //pin 13
#define a2Pin 8   //pin 14

Motor motor1 = Motor(0, 0, 0, 500, 90);  //global motor objects
Motor motor2 = Motor(0, 0, 1, 500, 90);
Motor motor3 = Motor(0, 1, 0, 500, 90);
Motor motor4 = Motor(0, 1, 1, 500, 90);
Motor motor5 = Motor(1, 0, 0, 500, 90);
Motor motor6 = Motor(1, 0, 1, 500, 90);

//LCD SCREEN//
DFRobot_RGBLCD1602 lcd(16, 2); //global lcd object

//BUTTONS//
#define button1 A3   //pin 26
#define button2 A2   //pin 25
volatile bool B1Flag = 0;  //Flags to be used by interrupt - goes high (1) when button is pushed
volatile bool B2Flag = 0;
#define button1Led A0  //pin 23
#define button2Led 5  //pin 11

//ENCODER BUTTON
#define buttonE A1   //pin 24
volatile bool BEFlag = 0;

//ENCODER
#define EncA 10  //pin 16
#define EncB 9   //pin 15
//volatile int lastEncPos = 0;  //stores previous encoder position
volatile bool CWFlag = 0;  //Clockwise flag  -  goes high when encoder rotated clockwise
volatile bool CCWFlag = 0;  //Counter-clockwise flag ...

//SYSTEM VARIABLES//
#define led 4  //onboard led  //pin 6
int speed = 50;   //controlled by encoder


void setup() {
  //START SERIAL PORT//
  Serial.begin(9600);
  Serial.println("Starting up");

  //LCD SCREEN INITIALIZATION//
  lcd.init();
  lcd.setRGB(100, 100, 100);
  lcd.setCursor(0, 0);
  lcd.print("Time:");
  lcd.setCursor(0, 1);  //for test debugging - display seconds in bottom left of screen
  lcd.print("Btn:"); //print seconds since startup
  lcd.setCursor(7, 1);  //for test debugging - display seconds in bottom left of screen
  lcd.print("Spe:"); //print seconds since startup
  lcd.print(speed);

  //MOTOR OUTPUT PIN DEFINITIONS//
  pinMode(stepPin, OUTPUT);
  pinMode(dirPin, OUTPUT);
  pinMode(a0Pin, OUTPUT);
  pinMode(a1Pin, OUTPUT);
  pinMode(a2Pin, OUTPUT);

  //BUTTON INPUT PIN DEFINTIONS AND INTERRUPTS// - (PIN CHANGE INTERRUPT)
  pinMode(button1, INPUT);  //using an external 4.7k pulldown resistor
  pinMode(button2, INPUT);
  pinMode(buttonE, INPUT);
  PCICR |= B00000010;  //Enable pin change interrupt on port C (A0-A5) (pins 23-28)
  PCMSK1 |= B00001110;  //Enable interrupts for pins A0-A2 (pins 24-26)

  //BUTTON LEDs
  pinMode(button1Led, OUTPUT);
  pinMode(button2Led, OUTPUT);

  //ENCODER INPUT PIN DEFINTIONS, INTERRUPTS, AND POSITION CONFIG//
  pinMode(EncA, INPUT);  //using an external 10k pullup resistor
  pinMode(EncB, INPUT);
  PCICR |= B00000001;  //Enable pin change interrupt on port B (D8-D13) (pins 14-19)
  PCMSK0 |= B00000100;  //Enable interrupts for pin D10 (pin 16, EncA)  //for old encoder:PCMSK0 |= B00000110;  //Enable interrupts for pins D9-D10 (pins 15-16)
  //lastEncPos = encoderInputToState(digitalRead(EncA), digitalRead(EncB)); //set to current (previous) position  //used with old encoder

  //LED
  pinMode(led, OUTPUT);
}

void loop() 
{
  lcd.setCursor(5, 0);  //for test debugging - display seconds in bottom left of screen
  lcd.print(millis()/1000); //print seconds since startup

  //PUSH BUTTON HANDLERS
  if(B1Flag == 1){
    lcd.setCursor(4,1);
    lcd.print("1");
    digitalWrite(button1Led, HIGH);
    delay(600);
    digitalWrite(button1Led, LOW);
    B1Flag = 0;
  }
  if(B2Flag == 1){
    lcd.setCursor(4,1);
    lcd.print("2");
    digitalWrite(button2Led, HIGH);
    delay(600);
    digitalWrite(button2Led, LOW);
    B2Flag = 0;
  }
  if(BEFlag == 1){
    lcd.setCursor(4,1);
    lcd.print("E");
    BEFlag = 0;
  }

  //ENCODER HANDLER
  if(CWFlag == 1){  //if encoder is rotates clockwise
    if(speed < 100)
      speed = speed + 5;
    lcd.setCursor(11,1);
    lcd.print("   ");
    lcd.setCursor(11,1);
    lcd.print(speed);
    CWFlag = 0;  //reset flag for next time
  }
  if(CCWFlag == 1){
     if(speed > 5)
      speed = speed - 5;
    lcd.setCursor(11,1);
    lcd.print("   ");
    lcd.setCursor(11,1);
    lcd.print(speed);
    CCWFlag = 0;  //reset flag for next time
  }



  //WAIT FOR AND PROCESS SERIAL STRING COMMAND//
  if(Serial.available())    //while (Serial.available() == 0) {}            //wait for serial string data available
  {
    String inputSequence = Serial.readString();   //read until timeout
    inputSequence.trim();                         // remove any \r \n whitespace at the end of the String
    int spaceIndex = 0;
    while(inputSequence.length() > 0)            //process through sequence string of face moves
    {
      spaceIndex = inputSequence.indexOf(" ");
      String tempFirst = inputSequence.substring(0, spaceIndex);    //find space separation, then find command up to first space
      Serial.print("Processing " + tempFirst + ":  ");
      decodeAndRunMotor(tempFirst);                                 //run motors based on first command in string     

      lcd.setCursor(14,1);  //display current command in bottom right of screen
      lcd.print("  ");
      lcd.print(tempFirst);

      if(spaceIndex == -1)
        inputSequence = "";
      else
        inputSequence = inputSequence.substring(spaceIndex + 1, inputSequence.length());    //remove first command from string and repeat
    }
  }

}


//interrupt service routine for all 3 buttons (A1-A3)
//flips flag for corresponding button
ISR (PCINT1_vect)
{
  if(digitalRead(button1) == HIGH)
    B1Flag = 1;
  else if(digitalRead(button2) == HIGH)
    B2Flag = 1;
  else if(digitalRead(buttonE) == HIGH)
    BEFlag = 1;
}

//interrupt service routine for encoder (D10, EncA)
ISR (PCINT0_vect)  //called for any change in A, so verify rising, then see what B currently is
{
  if(digitalRead(EncA) == HIGH) //if A is rising
  {
    if(digitalRead(EncB) == HIGH) //if B has risen, must be CCW
      CCWFlag = 1;
    else                  //if B has fallen, must be CW
      CWFlag = 1;
  }
  /*  //old encoder
  //interrupt service routine for encoder (D9-D10)
  //flips direction flag based encoder inputs (previous and current state)
  //Position(Pos) STATES: 0,1,2,3
  int currentEncPos = encoderInputToState(digitalRead(EncA), digitalRead(EncB));
  if(currentEncPos == ((lastEncPos+1)%4)) //CW
    CWFlag = 1;
  else   //must be CCW
    CCWFlag = 1;
  lastEncPos = currentEncPos;
  */
}


//translates the 2 inputs for the encoder into a predefined state 
//STATE = AB: 0=00, 1=10, 2=11, 3=01
/*
int encoderInputToState(bool A, bool B)
{
  if(A == false){
    if(B == false)
      return 0;  //00
    else
      return 3;  //01
  }
  else{
    if(B == false)
      return 1;  //10
    else
      return 2;  //11
  }
}
* */
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

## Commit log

2022-12-03 Mounting Seq Complete
2022-12-07 final CV static capture updates for enclosure
